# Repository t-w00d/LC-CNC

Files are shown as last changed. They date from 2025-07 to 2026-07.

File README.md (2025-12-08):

# Low-Cost CNC Desktop Milling Machine
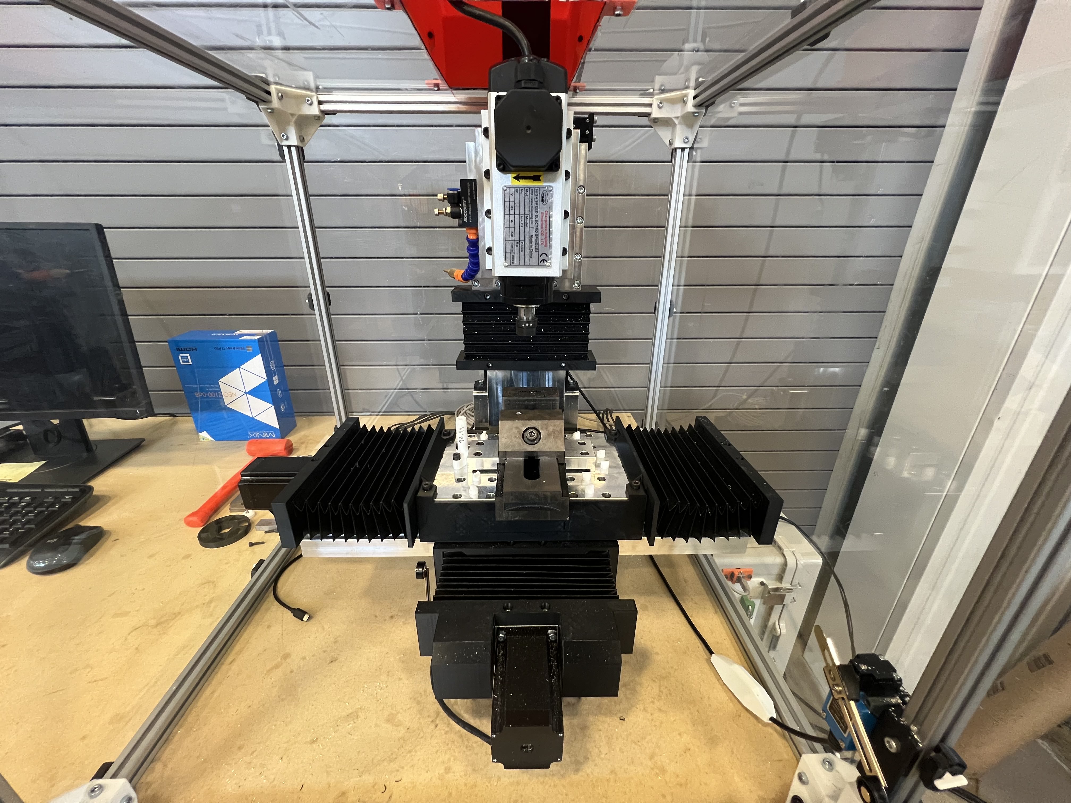
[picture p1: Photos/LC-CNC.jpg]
LC CNC Photo

# 

# |LC-CNC|

# This repository contains all necessary design files, instruction documents, and software binaries to build and run a low-cost desktop CNC machine. It includes: 

# \- Mechanical/Electrical design (SolidWorks files)
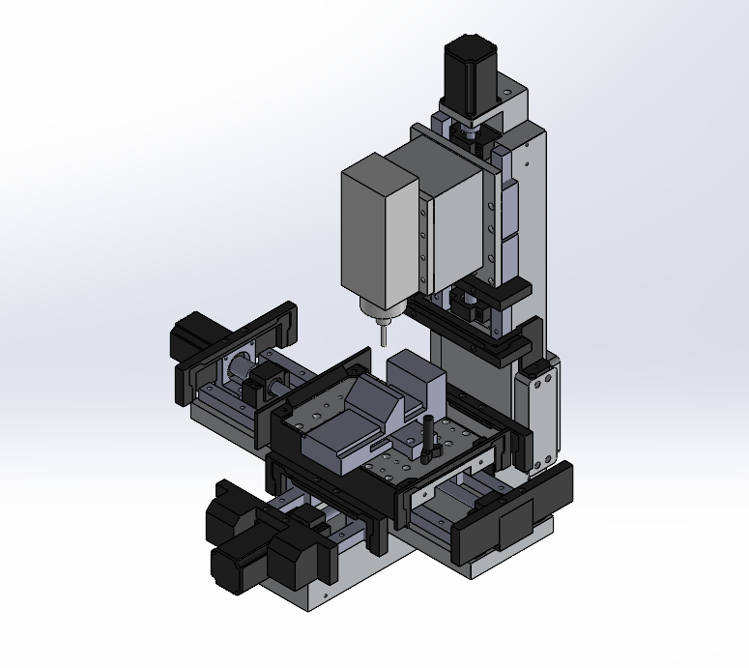
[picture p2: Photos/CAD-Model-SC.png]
CAD Model

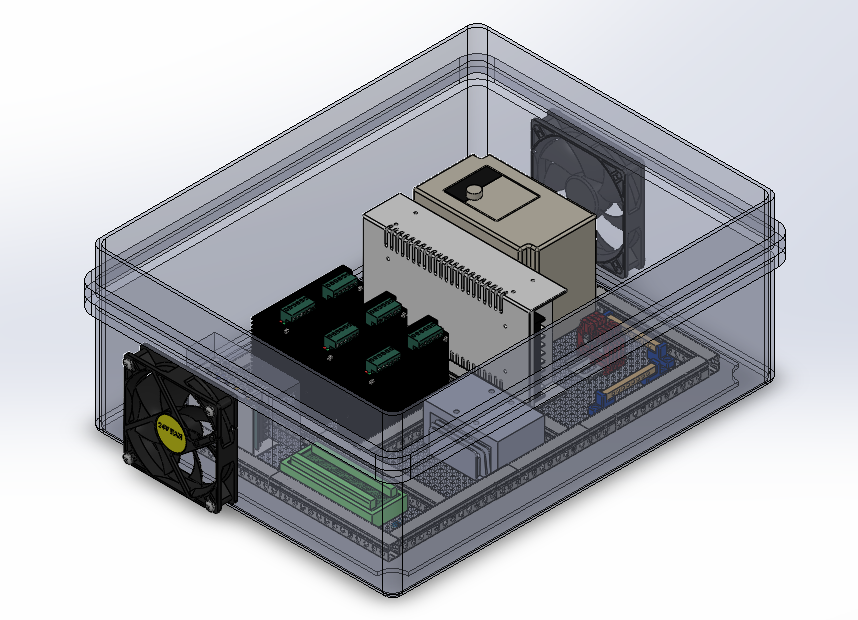
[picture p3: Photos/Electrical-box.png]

# \- Assembly + wiring instructions
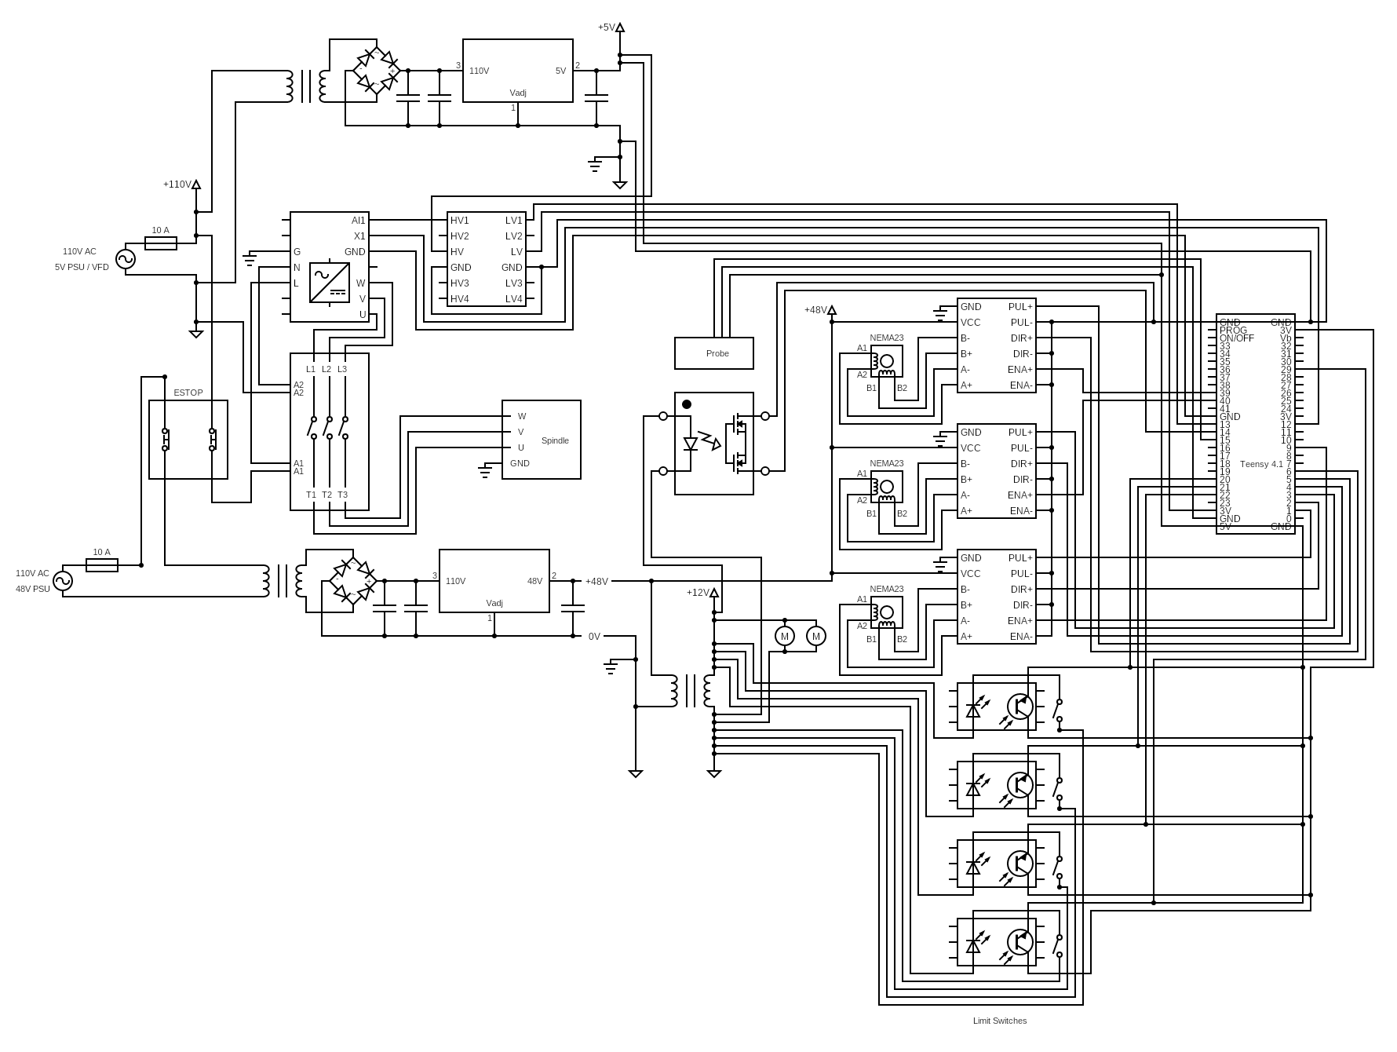
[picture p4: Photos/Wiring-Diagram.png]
Wiring Diagram

# \- Open-source firmware and control software for ease of use
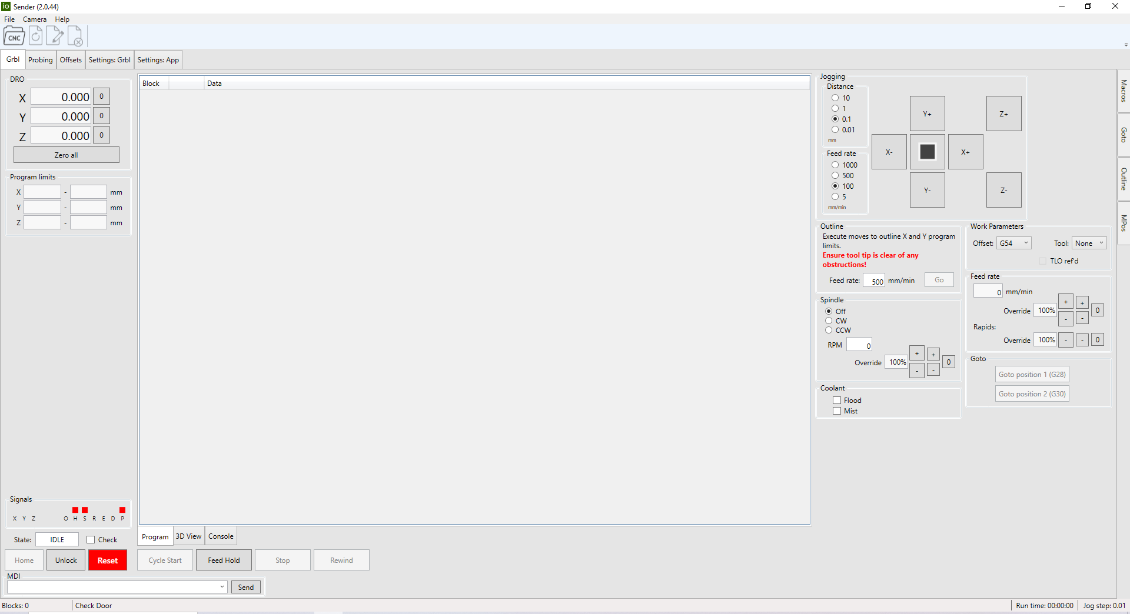
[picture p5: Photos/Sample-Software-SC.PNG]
Sender Software

# \- Educational curriculum tailored for the machine
# \- Bill of Materials
# \- Performance evaluations (error motions and circle-diamond-square)
# \- User manuals and datasheets

# |Specs|
# Current version uses machined 6061-T6 aluminum for the base, saddle, and column
# Driven by NEMA 23 motors with 2.45 N-m holding torque and DM556/DM566 drivers
# Motion system includes 16 mm ball screws and HGR20 linear rails for all axes
# 2.2 kW air-cooled spindle requires a VFD but runs on standard 110 V supply
# Controller is a Teensy 4.1 running GRBLHAL for machine control and compensation
# Machine footprint is roughly 660 mm x 660 mm
# Work volume: 152 mm x 254 mm x 152 mm 

# |Purchasing| (CNC-BoM.xlsx.)

# - All Machine/Electrical Components are required for the assembly of the LC-CNC

#	NOTE: The link to the carts are provided for ease of purchase when possible

# - All tools are required for successful assembly of the LC-CNC 

#	NOTE: Most tools are standard so only buy the specific tools you do not own

# - Recommendations are optional and only slightly improve user experience

#	NOTE: The table for the machine must be able to support 150lbs.

#	NOTE: Computer requirements: OS-Windows 10/11; Must have an ethernet port

#

# |Downloads|

# To avoid the need to navigate external GitHub repositories, the following software is bundled in the `binaries/` folder:

# -teensy.exe
# -ioSender.XL.2.0.46.zip
# -firmware.hex

# Download these versions that are known to work with the mechanical and electrical configuration provided in this repository. No modifications were made to the source code.

#

# |Getting Started|

# 1\. Purchase necessary items from CNC-BoM.xlsx.

# 2\. Assemble your machine using the instructions

# 3\. Flash `.hex` to your Teensy 4.1 using any Teensy-compatible flashing tool (teensy.exe)

# 4\. Download and extract `ioSender` from the provided ZIP

# 5\. Connect to your machine, configure settings, and start cutting! 

#

# |Educational Use|

# This project is tailored for use in schools, makerspaces, and research labs. The provided curriculum aligns with design and performance of this specific machine.

# We welcome improvements to documentation or curriculum under the same license terms.

#

# |License|

# All original work in this repository (CAD files, documentation, and curriculum) is licensed under the \*\*Creative Commons Attribution-NonCommercial-ShareAlike 4.0 International License (CC BY-NC-SA 4.0)\*\*.

# Read the full license terms here: https://creativecommons.org/licenses/by-nc-sa/4.0/ 

#

# |Third-Party Software|

# See `THIRD\_PARTY\_LICENSES.txt` for licensing details of the included firmware and sender application.

# \- grblHAL (GPL-3.0+)

# https://github.com/grblHAL

# \- ioSender (BSD-3-Clause)

# https://github.com/terjeio/ioSender

#

# |Credits|

# \- Original mechanical design and curriculum by Tyler Woodard, John Greene, and Colby Hale

# \- Firmware and sender software by Terje Io

# 

# Please respect original licenses when redistributing.

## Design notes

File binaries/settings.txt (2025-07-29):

%
;
; 2025-07-28T14:59
;
; grblHAL
; 1.1f.20250611
; [OPT:VNMSL+,100,1024,3,0]
; [NEWOPT:ENUMS,RT+,HOME,PROBES=1,ES,REBOOT,SED,ETH]
; [FIRMWARE:grblHAL]
; [NVS STORAGE:*FLASH]
; [FREE MEMORY:480K]
; [DRIVER:iMXRT1062]
; [DRIVER VERSION:250528]
; [DRIVER OPTIONS:USB.1]
; [BOARD:T41U5XBB]
; [AUX IO:6,3,0,0]
; [IP:169.254.28.238]
; [NETCON:Telnet]
;
$N0=
$N1=
; 0 - Step pulse time
$0=10.0
; 1 - Step idle delay
$1=25
; 2 - Step pulse invert
$2=0
; 3 - Step direction invert
$3=0
; 4 - Invert stepper enable output(s)
$4=7
; 5 - Invert limit inputs
$5=7
; 6 - Invert probe inputs
$6=1
; 9 - PWM spindle options
$9=1
; 10 - Status report options
$10=511
; 11 - Junction deviation
$11=0.010
; 12 - Arc tolerance
$12=0.002
; 13 - Report in inches
$13=0
; 14 - Invert control inputs
$14=8
; 15 - Invert coolant outputs
$15=0
; 16 - Invert spindle signals
$16=0
; 17 - Pullup disable control inputs
$17=0
; 18 - Pullup disable limit inputs
$18=0
; 19 - Pullup disable probe inputs
$19=0
; 20 - Soft limits enable
$20=0
; 21 - Hard limits enable
$21=0
; 22 - Homing cycle
$22=1
; 23 - Homing direction invert
$23=0
; 24 - Homing locate feed rate
$24=100.0
; 25 - Homing search seek rate
$25=500.0
; 26 - Homing switch debounce delay
$26=250
; 27 - Homing switch pull-off distance
$27=12.700
; 28 - G73 Retract distance
$28=0.100
; 29 - Pulse delay
$29=0.0
; 30 - Maximum spindle speed
$30=24000.000
; 31 - Minimum spindle speed
$31=0.000
; 32 - Mode of operation
$32=0
; 33 - Spindle PWM frequency
$33=5000
; 34 - Spindle PWM off value
$34=0.0
; 35 - Spindle PWM min value
$35=0.0
; 36 - Spindle PWM max value
$36=100.0
; 37 - Steppers to keep enabled
$37=0
; 39 - Enable legacy RT commands
$39=1
; 40 - Limit jog commands
$40=0
; 41 - Parking cycle
$41=0
; 42 - Parking axis
$42=2
; 43 - Homing passes
$43=1
; 44 - Axes homing, first pass
$44=4
; 45 - Axes homing, second pass
$45=3
; 46 - Axes homing, third pass
$46=0
; 56 - Parking pull-out distance
$56=5.0
; 57 - Parking pull-out rate
$57=100.0
; 58 - Parking target
$58=-5.0
; 59 - Parking fast rate
$59=500.0
; 60 - Restore overrides
$60=0
; 61 - Safety door options
$61=0
; 62 - Sleep enable
$62=0
; 63 - Feed hold actions
$63=3
; 64 - Force init alarm
$64=0
; 65 - Probing options
$65=0
; 70 - Network Services
$70=1
; 100 - X-axis travel resolution
$100=640.000
; 101 - Y-axis travel resolution
$101=640.000
; 102 - Z-axis travel resolution
$102=640.000
; 110 - X-axis maximum rate
$110=7500.000
; 111 - Y-axis maximum rate
$111=7500.000
; 112 - Z-axis maximum rate
$112=7500.000
; 120 - X-axis acceleration
$120=250.000
; 121 - Y-axis acceleration
$121=250.000
; 122 - Z-axis acceleration
$122=250.000
; 130 - X-axis maximum travel
$130=200.000
; 131 - Y-axis maximum travel
$131=200.000
; 132 - Z-axis maximum travel
$132=200.000
; 160 - X-axis backlash compensation
$160=0.013
; 161 - Y-axis backlash compensation
$161=0.013
; 162 - Z-axis backlash compensation
$162=0.000
; 300 - Hostname
$300=grblHAL
; 301 - IP Mode
$301=0
; 302 - IP Address
$302=169.254.28.238
; 303 - Gateway
$303=169.254.28.1
; 304 - Netmask
$304=255.255.0.0
; 305 - Telnet port
$305=23
; 307 - Websocket port
$307=80
; 341 - Tool change mode
$341=0
; 342 - Tool change probing distance
$342=30.0
; 343 - Tool change locate feed rate
$343=25.0
; 344 - Tool change search seek rate
$344=200.0
; 345 - Tool change probe pull-off rate
$345=200.0
; 346 - Tool change options
$346=1
; 370 - Invert I/O Port inputs
$370=0
; 372 - Invert I/O Port outputs
$372=0
; 384 - Disable G92 persistence
$384=0
; 392 - Spindle on delay
$392=4.0
; 393 - Coolant on delay
$393=1.0
; 394 - Spindle on delay
$394=0.0
; 398 - Planner buffer blocks
$398=100
; 481 - Autoreport interval
$481=0
; 484 - Unlock required after E-Stop
$484=0
; 486 - Lock coordinate systems
$486=0
; 539 - Spindle off delay
$539=0.0
; 673 - Coolant on delay
$673=0.0
; 676 - Reset actions
$676=3
; 680 - Stepper enable delay
$680=0
%

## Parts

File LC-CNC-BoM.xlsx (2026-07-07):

Machine/Electrical Components: |  | Number of Machines: |  |  | 1 | Tools | NOTE: Only one set of tools needed
Item | Link | Status | Quantity | Price/Item | Total Price | Item | Link | Status | Quantity | Price/Item | Total Price
Makerstore |  |  |  |  |  | Amazon
Shielded 4 Core Cable – 22AWG | https://makerstore.cc/product/elec-cable-4s-xtension/ | In Stock | 15 | $3.33 | $49.95 | Ferrule crimping tool | https://www.amazon.com/Klein-Tools-34056-Adjustable-Electrical/dp/B0D98N52HS | In Stock | 1 | $20.99 | $20.99
Shielded 2 Core Cable – 22AWG | https://makerstore.cc/product/elec-cable-2s-xtension/ | In Stock | 15 | $1.73 | $25.95 | Ferrule connectors | https://www.amazon.com/Fidioto-Terminals-Connector-Insulated-Industrial/dp/B09XQN3J6N?s=industrial | In Stock | 1 | $14.99 | $14.99
Amazon |  |  |  |  |  | Soldering iron | https://www.amazon.com/gp/product/B0CJR4Y192/ref=ox_sc_act_title_2?smid=A1NCCSMTWFDZ34&psc=1 | In Stock | 1 | $19.99 | $19.99
110v Spindle Motor Kit，2.2Kw Square Air Cooled Spindle Motor 24000Rpm 400Hz ，VFD Variable Frequency Drive ，7 pcs ER11 Collets | https://a.co/d/04KkNO5x | In Stock | 1 | $359.99 | $359.99 | Solder | https://www.amazon.com/MAIYUM-63-37-Solder-Electrical-Soldering/dp/B075WB98FJ?s=hi | In Stock | 1 | $8.99 | $8.99
16awg 4 core wire 12ft | https://www.amazon.com/Shielded-Extreme-Flexible-Electrical-Machine/dp/B0C1YH4J1T | In Stock | 1 | $30.99 | $30.99 | Heat shrink | https://www.amazon.com/Ginsco-580-pcs-Assorted-Sleeving/dp/B01MFA3OFA?s=industrial | In Stock | 1 | $6.99 | $6.99
 |  |  |  |  |  | Heat gun | https://www.amazon.com/Wagner-Spraytech-2417344-Included-Settings/dp/B08RHDWTW1?s=industrial | In Stock | 1 | $27.99 | $27.99
Way Covers | https://www.amazon.com/dp/B07BXK6BYS?s=hi&sp_csd=d2lkZ2V0TmFtZT1zcF9kZXRhaWw | In Stock | 4 | $20.18 | $80.72 | Manual Wire stripper | https://www.amazon.com/VISE-GRIP-Stripping-Cutter-8-Inch-2078309/dp/B000JNNWQ2?s=industrial | In Stock | 1 | $13.33 | $13.33
Air blast | https://www.amazon.com/Upgrade-Version-Coolant-Lubrication-Engraving/dp/B07X89Z1W9?hvadid=616989210950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 | In Stock | 1 | $18.88 | $18.88 | Crimp tool | https://www.amazon.com/Haisstronica-Electrical-Connectors-AWG-Tools-Racheting-Tools-Available/dp/B08F3JKDD3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 | In Stock | 1 | $18.69 | $18.69
5 Pin connector | https://www.amazon.com/DaFurui-5-08mm-Screw%EF%BC%8C10Pcs-Terminal-Connector/dp/B0C2XZFR1J?s=industrial | In Stock | 1 | $16.99 | $16.99 | Stub Allen Key set | https://www.amazon.com/Powerbuilt-Piece-Stubby-Long-Wrench/dp/B07N8F7W7K | In Stock | 1 | $24.99 | $24.99
3 Pin connector | https://www.amazon.com/DaFurui-5-08mm-Screw%EF%BC%8C10Pcs-Terminal-Connector/dp/B0C2Y2V78Y?s=industrial | In Stock | 1 | $16.99 | $16.99 | Screw driver set | https://www.amazon.com/Amazon-Basics-Ratcheting-Electronics-Screwdriver/dp/B07V4TFWFZ?s=industrial | In Stock | 1 | $15.09 | $15.09
Loctite-Blue | https://www.amazon.com/Loctite-Heavy-Duty-Threadlocker-Single/dp/B000I1RSNS | In stock | 1 | $7.24 | $7.24 | Automatic Wire stripper | https://www.amazon.com/WEICON-Stripper-Adjustable-0-2-6-0-Stripping/dp/B001NUMVHQ | In Stock | 1 | $25.50 | $25.50
Touch Probe | https://www.amazon.com/V5-Waterproof-Anti-roll-Compatible-Finder-NO/dp/B0BDSDSJF6 | In stock | 1 | $67.99 | $67.99 | Compressor | https://www.amazon.com/Milwaukee-M12-Lithium-Ion-Cordless-Kit/dp/B07J1DCM59?s=hi | In Stock | 1 | $162.00 | $162.00
Ethernet cable | https://www.amazon.com/Amazon-Basics-Ethernet-High-Speed-Snagless/dp/B089MGH8W3?s=electronics | In Stock | 1 | $6.39 | $6.39 | Magnets | https://www.amazon.com/AplysiaTech-N52-3-Powerful-Neodymium-Scientific/dp/B0DC65Z3SF?ref_=ast_sto_dp | In Stock | 1 | $23.99 | $23.99
Fans | https://www.amazon.com/Strong-120x120x25mm-Computer-Cooling-1600RPM/dp/B07D493BDX | In Stock | 1 | $12.99 | $12.99 | Ferrite beads | https://www.amazon.com/HUAREW-Values-Ferrite-Suppressor-Diameter/dp/B09SWNPY2Y | In Stock | 1 | $13.99 | $13.99
Limit Switches | https://www.amazon.com/dp/B07PZ1WB8S?psc=1&smid=A26VZBPE6PT1GF&ref_=chk_typ_imgToDp | In Stock | 1 | $9.99 | $9.99 | Hammer | https://www.amazon.com/Neiko-02846A-Hammer-Orange-Handle/dp/B002GQ967Y?ref_=ast_sto_dp&th=1 | In Stock | 1 | $12.81 | $12.81
PSU 0-48v 0-10A | https://www.amazon.com/DROK-110V-220V-Converter-Adjustable-Transformer/dp/B08GFQZFC1?s=electronics | In Stock | 1 | $39.99 | $39.99 | Multimeter | https://www.amazon.com/Klein-Tools-MM325-Multimeter-Manual-Ranging/dp/B0B57L9FNL | In Stock | 1 | $34.97 | $34.97
300mm Ball screw | https://www.amazon.com/CHUANGNENG-Deflector-Supports-HOUSINGS-Machining/dp/B089DF7P6R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 | 4 In Stock (4-13-25) | 2 | $34.69 | $69.38 | McMaster Carr
450mm Ball screw | https://www.amazon.com/CHUANGNENG-Deflector-Supports-HOUSINGS-Machining/dp/B089DGRFY9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 | 8 In Stock (4-13-25) | 1 | $40.39 | $40.39 | T handle | https://www.mcmaster.com/5374A56/ | In Stock | 1 | $9.54 | $9.54
48v to 12v step down | https://www.amazon.com/KInuoxj-Converter-Regulator-Waterproof-Transformer/dp/B0CS2KJSKS | In Stock | 1 | $16.99 | $16.99 | Grease gun | https://www.mcmaster.com/1190K37/ | In Stock | 1 | $41.86 | $41.86
4pcs 8 position grounding bar | https://www.amazon.com/gp/product/B0CYHH6ZPM/ref=ewc_pr_img_8?smid=A2UXHIGK0EM1ZO&psc=1 | In Stock | 1 | $8.99 | $8.99 | Wire Stripper | https://www.mcmaster.com/7312K11/ | In Stock | 1 | $36.15 | $36.15
4 pack DM566 drivers | https://www.amazon.com/Digital-Stepper-Controller-2-Phase-Subdivision/dp/B0CN41Y4DJ | 11 In Stock (4-13-25) | 1 | $48.99 | $48.99 | Allen key set | https://www.mcmaster.com/5709A44/ | In Stock | 1 | $7.55 | $7.55
300PCS Electrical Connectors Kit, | https://www.amazon.com/gp/product/B086ZP4N7K/ref=ox_sc_act_title_7?smid=AON9H44N0KDA1&th=1 | In Stock | 1 | $8.99 | $8.99 | MSC
3'' Precision Screwless Vise | https://www.amazon.com/AccusizeTools-Precision-Screwless-Hardened-0235-0303/dp/B00UCHGLUO | 16 In Stock (4-13-25) | 1 | $124.00 | $124.00 | 1-2-3 setup block | https://www.mscdirect.com/product/details/03433620 | In Stock | 1 | $55.35 | $55.35
Roller arm Limit Switches | https://a.co/d/0cbCCCRe | In Stock | 2 | $8.99 | $17.98 | Square Steel Gage: .35 in | https://www.mscdirect.com/product/details/86274404 | In Stock | 1 | $35.76 | $35.76
 |  |  |  |  |  | Square Steel Gage: .13 in | https://www.mscdirect.com/product/details/86272507 | In Stock | 1 | $30.07 | $30.07
 |  |  |  |  |  | Gage pin | https://www.mscdirect.com/product/details/89024806 | In Stock | 1 | $3.80 | $3.80
22awg wire | https://www.amazon.com/TYUMEN-Hookup-Electrical-Strips-Extension/dp/B07SLBD1FY?s=industrial | In Stock | 1 | $15.99 | $15.99 | Indicator positioner | https://www.mscdirect.com/product/details/94110061 | In Stock | 1 | $87.75 | $87.75
Logic level shifter | https://www.amazon.com/HiLetgo-Channels-Converter-Bi-Directional-3-3V-5V/dp/B07F7W91LC?s=industrial | In Stock | 1 | $7.69 | $7.69 | Calipers | https://www.mscdirect.com/product/details/62529482 | In Stock | 1 | $148.53 | $148.53
Heat set assortment | https://www.amazon.com/dp/B08ZJ6HNGK?ref_=ppx_hzsearch_conn_dt_b_fed_asin_title_1&th=1 | In Stock | 1 | $11.47 | $11.47 | Indicator | https://www.mscdirect.com/product/details/38353306 | In Stock | 1 | $171.00 | $171.00
10A 16awg fuse | https://www.amazon.com/16-AWG-Inline-Fuse-Holder/dp/B08K3NFZCP?ref_=ast_sto_dp&th=1 | In Stock | 1 | $12.99 | $12.99 | Shop vac | https://www.mscdirect.com/product/details/16520850 | In Stock | 1 | $84.66 | $84.66
Optocoupler Isolation Board | https://www.amazon.com/dp/B07TCVTD2K?ref=ppx_yo2ov_dt_b_fed_asin_title&th=1 | In Stock | 1 | $7.99 | $7.99 | Parallel set | https://www.mscdirect.com/product/details/06820898 | In Stock | 1 | $102.36 | $102.36
1CH Optocoupler isolation board | https://www.amazon.com/dp/B01L1OI1HC?ref_=ppx_hzsearch_conn_dt_b_fed_asin_title_4&th=1 | In Stock | 1 | $13.99 | $13.99 | Total |  |  |  |  | $1259.68
L Connector brackets | https://www.amazon.com/gp/product/B0BY51FJGY/ref=ewc_pr_img_1?smid=AO6JMNGOG26ZH&th=1 | In Stock | 2 | $19.99 | $39.98
5V Power Supply | https://www.amazon.com/Universal-Regulated-Switching-Converter-Transformer/dp/B07PPPF1R5 | In Stock | 1 | $10.07 | $10.07 | Crank Slider Stock | NOTE: This qty will make 16 assemblies
4 Pin Terminal Block | https://a.co/d/07VW1Jxs | In Stock | 1 | $9.99 | $9.99 | Item | Link | Status | Quantity | Price/Item | Total Price
NEMA 23 Stepper motor 3N-m | https://www.amazon.com/gp/product/B00PNEPW4C/ref=ox_sc_act_title_22?smid=AWQBCGWISS7BL&psc=1 | In Stock | 1 | $39.99 | $39.99 | McMaster
NEMA 23 Stepper motor 2.4N-m | https://a.co/d/0cYAOFF7 | In Stock | 2 | $25.99 | $51.98 | Base Stock 4ft | https://www.mcmaster.com/8662K88/ | In Stock | 1 | $77.32 | $77.32
8mm to 10mm Shaft Coupling | https://a.co/d/0c78GAUY | In Stock | 1 | $12.99 | $12.99 | Crank Stock 3ft | https://www.mcmaster.com/8975K12-8975K123/ | In Stock | 1 | $22.81 | $22.81
Teensy 4.1 Ethernet Kit | https://a.co/d/04Kofe6e | In Stock | 1 | $13.95 | $13.95 | Slider Stock 3ft | https://www.mcmaster.com/9008K11-9008K113/ | In Stock | 1 | $16.12 | $16.12
Teensy 4.1 Conrtoller | https://www.amazon.com/gp/product/B08CTM3279/ref=ox_sc_act_title_5?smid=A2GTSJRNFEVVSP&psc=1 | In Stock | 1 | $44.15 | $44.15 | ER20 Collet - 1/4 in | https://www.mcmaster.com/1724N17/ | In Stock | 1 | $53.00 | $53.00
10mm to 10mm Shaft Coupling | https://a.co/d/0aCp7x5M | In Stock | 1 | $12.99 | $12.99 | ER20 Collet - 1/8 in | https://www.mcmaster.com/1724N13/ | In Stock | 1 | $53.00 | $53.00
Digikey |  |  |  |  |  | MSC
2 Pin PCB terminal block | https://www.digikey.com/en/products/detail/w-rth-elektronik/691210910002/10668428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 | In Stock | 10 | $0.89 | $8.86 | 1/8th inch square endmill | https://www.mscdirect.com/product/details/65249682 | In Stock | 2 | $19.63 | $39.26
McMaster Carr |  |  |  |  |  | 1/4th inch square endmill | https://www.mscdirect.com/product/details/82976580 | In Stock | 2 | $28.81 | $57.62
IEC Receptical | https://www.mcmaster.com/5428N111/ | In Stock | 2 | $14.77 | $29.54 | Total: |  |  |  |  | $319.13
IEC Cable | https://www.mcmaster.com/71535K51/ | In Stock | 2 | $7.80 | $15.60
Hinges | https://www.mcmaster.com/6812N511/ | In Stock | 2 | $13.05 | $26.10 | Recommendedations | NOTE: Computer must have ethernet
EP1 Grease | https://www.mcmaster.com/1416K41/ | In Stock | 1 | $9.01 | $9.01 | Item | Link | Status | Quantity | Price/Item | Total Price
Vibration-Damping Sandwich Mount with Stud&Insert | https://www.mcmaster.com/93945K155/ | In Stock | 4 | $3.81 | $15.24 | McMaster
Touch plate screw | https://www.mcmaster.com/99607A263/ | In Stock | 1 | $5.29 | $5.29 | Table option 1 | https://www.mcmaster.com/6682T93/ | In Stock | 1 | $721.96 | $721.96
T-Nuts | https://www.mcmaster.com/5537T651/ | In Stock | 10 | $4.18 | $41.80 | MSC
Polycarbonate sheet | https://www.mcmaster.com/8574K53/ | In Stock | 2 | $30.67 | $61.34 | Table option 2 | https://www.mscdirect.com/product/details/51724680 | In Stock | 1 | $367.84 | $367.84
M5x12 mm bolts | https://www.mcmaster.com/90128A236/ | In Stock | 2 | $9.55 | $19.10 | Best Buy
M5x16 mm bolts | https://www.mcmaster.com/91290A232/ | In Stock | 1 | $16.87 | $16.87 | Computer | https://www.bestbuy.com/site/minix-z100-0db-fanless-mini-pc-intel-12th-gen-n100-16gb-ddr4-512gb-pcie-gen3-x-4-nvme-ssd-windows-11-pro-desktop-computer-black/6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 | In Stock | 1 | $239.99 | $239.99
1/4-20 bolts -1.25in | https://www.mcmaster.com/90128A250/ | In Stock | 1 | $8.33 | $8.33 | Total: |  |  |  |  | $961.95
1/4-20 bolts -1-5/8in | https://www.mcmaster.com/91251A527/ | In Stock | 1 | $20.87 | $20.87
1/4-20 bolts -.75in | https://www.mcmaster.com/91251A540/ | In Stock | 2 | $11.38 | $22.76 | Stock material | NOTE: Local metal supplier to UTK; Price per 1 machine
M5x25 mm bolts | https://www.mcmaster.com/91290A252/ | In Stock | 1 | $10.71 | $10.71 | Item | Link | Status | Quantity | Price/Item | Total Price
1/4-20 bolts -1in | https://www.mcmaster.com/91251A542/ | In Stock | 1 | $12.36 | $12.36 | Specialty Metals
M5x40 mm bolts | https://www.mcmaster.com/91290A196/ | In Stock | 1 | $7.78 | $7.78 | 6061 1" x 6" | N/a | In Stock | 1 | $135.00 | $135.00
M3x10mm | https://www.mcmaster.com/91290A115/ | In Stock | 1 | $12.92 | $12.92 | 6061 2.5" x 5" | N/a | In Stock | 1 | $280.00 | $280.00
M3x10mm self tap | https://www.mcmaster.com/99461A942/ | In Stock | 1 | $8.00 | $8.00 | 6061 3.5" x 6" | N/a | In Stock | 1 | $102.00 | $102.00
M4x16 mm | https://www.mcmaster.com/91290A154/ | In Stock | 1 | $13.40 | $13.40 | Total: |  |  |  |  | $517.00
M4 hex nut | https://www.mcmaster.com/90591A255/ | In Stock | 1 | $3.11 | $3.11
M5 hex nut | https://www.mcmaster.com/90591A260/ | In Stock | 1 | $3.56 | $3.56 | Safety Stickers/PPE | NOTE: This qty is for 15 machines
#6 screws | https://www.mcmaster.com/90031A151/ | In Stock | 1 | $6.69 | $6.69 | Item | Link | Status | Quantity | Price/Item | Total Price
Twin ferrule assortment | https://www.mcmaster.com/9689K13/ | In Stock | 1 | $27.76 | $27.76 | MySafetyLabels
Shim stock | https://www.mcmaster.com/9504K321/ | In Stock | 1 | $15.31 | $15.31 | 1.5" x 3" ANSI Caution Safety Label: Eye protection required. (LB-0321) | https://www.mysafetylabels.com/msl/caution-eye-protection-required-safety-label/sku-lb-0321 | In Stock | 15 | $2.32 | $34.80
Washer assortment | https://www.mcmaster.com/91535A200/ | In Stock | 1 | $20.00 | $20.00 | 1.5" x 3" Hand Cut Warning Label: Moving Parts Can Crush And Cut, Do Not Operate With Guard Removed, Lockout/Tagout Before Servicing (LB-0231) | https://www.mysafetylabels.com/warning-labels/rotating-cutter-safety-label/sku-lb-0199 | In Stock | 15 | $2.32 | $34.80
Steel DIN 3 Rail, 2" Length | https://www.mcmaster.com/8961K84/ | In Stock | 1 | $3.90 | $3.90 | .75" x .84" ANSI Z535.4 and ISO 3864-2 Warning (Triangle) Safety Label: ISO W017 - Burn Hazard / Hot Surface (LB-0290) | https://www.mysafetylabels.com/warning-labels/burn-hazard-hot-surface-safety-label/sku-lb-0290 | In Stock | 24 | $1.79 | $42.96
Black DIN-Rail Terminal Block | https://www.mcmaster.com/7641K921-7641K929/ | In Stock | 2 | $2.34 | $4.68 | 1.5" x 3" ANSI Warning Label: Do Not Open | https://www.mysafetylabels.com/do-not-open-while-machine-is-in-operation-warning-label/sku-lb-2432 | In Stock | 15 | $2.32 | $34.80
Orange DIN-Rail Terminal Block | https://www.mcmaster.com/7641K921-7641K928/ | In Stock | 3 | $2.34 | $7.02 | 2"x 3" ANSI Z535.4 and ISO 3864-2 Warning (Triangle) Safety Label: ISO W012 - Electrical Shock / Electrocution (LB-0012) | https://www.mysafetylabels.com/115-volts-ansi-danger-label/sku-lb-2396-115 | In Stock | 24 | $1.11 | $26.64
Yellow DIN-Rail Terminal Block | https://www.mcmaster.com/7641K921-7641K927/ | In Stock | 3 | $2.34 | $7.02 | ULINE
White DIN-Rail Terminal Block | https://www.mcmaster.com/7641K921-7641K926/ | In Stock | 2 | $2.34 | $4.68 | Safety glasses | https://www.uline.com/Product/Detail/S-13390C/Safety-Glasses/Ice-Wraparounds-Clear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 | In Stock | 15 | $2.50 | $37.50
Wire ducts | https://www.mcmaster.com/7578K112-7578K725/ | In Stock | 1 | $23.68 | $23.68 | Lockout Tagout | https://www.uline.com/Product/Detail/H-3437/Lockout-Tagout/Electrical-Plug-Prong-Lockout | In Stock | 8 | $14.00 | $112.00
Zip tie anchor | https://www.mcmaster.com/7566K205/ | In Stock | 1 | $15.54 | $15.54 | Padlock | https://www.uline.com/Product/Detail/H-8621R/Lockout-Tagout/Uline-Lockout-Padlock-Keyed-Different-1-1-2-Shackle-Red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 | In Stock | 8 | $11.00 | $88.00
Cord grip | https://www.mcmaster.com/69915K53/ | In Stock | 2 | $4.79 | $9.58 | Total: |  |  |  |  | $411.50
Green 22 AWG Wire: Solid Core | https://www.mcmaster.com/8251T2-8251T351/ | In Stock | 1 | $3.64 | $3.64
Red 22 AWG Wire: Solid Core | https://www.mcmaster.com/8251T2-8251T391/ | In Stock | 1 | $3.64 | $3.64
Blue 22 AWG Wire: Solid Core | https://www.mcmaster.com/8251T2-8251T321/ | In Stock | 1 | $3.64 | $3.64
Orange 22 AWG Wire: Solid Core | https://www.mcmaster.com/8251T2-8251T371/ | In Stock | 1 | $3.64 | $3.64
Black 16 AWG Wire: Stranded | https://www.mcmaster.com/8054T16-8054T317/ | In Stock | 1 | $15.26 | $15.26
Red 16 AWG Wire: Stranded | https://www.mcmaster.com/8054T16-8054T361/ | In Stock | 1 | $8.16 | $8.16
White 16 AWG Wire: Stranded | https://www.mcmaster.com/8054T16-8054T366/ | In Stock | 1 | $8.16 | $8.16
Green 16 AWG Wire: Stranded | https://www.mcmaster.com/8054T16-8054T338/ | In Stock | 1 | $8.16 | $8.16
Emergency Stop | https://www.mcmaster.com/6785K22/ | In Stock | 1 | $85.17 | $85.17
80/20
20-2020 LENGTH: 596.6 millimeters | https://8020.net/20-2020.html | In Stock | 8 | $9.07 | $72.56
20-2020 LENGTH: 636.6 millimeters | https://8020.net/20-2020.html | In Stock | 4 | $9.49 | $37.96
20-2020 LENGTH: 593.6 millimeters | https://8020.net/20-2020.html | In Stock | 2 | $9.04 | $18.08
20-2020 LENGTH: 553.6 millimeters | https://8020.net/20-2020.html | In Stock | 2 | $8.63 | $17.26
14157 LENGTH: 8 meters | https://8020.net/14157.html | In Stock | 1 | $28.24 | $28.24
CZH-LABS
Breakout board | https://czh-labs.com/products/terminal-block-breakout-board-module-for-teensy-41-screw-mount-version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 | In Stock | 1 | $20.90 | $20.90
Grainger
DAYTON Definite Purpose Magnetic Contactor | https://www.grainger.com/product/DAYTON-Definite-Purpose-Magnetic-783Y04 | In stock | 1 | $30.21 | $30.21
Component Total: |  |  |  |  | $2270.06
Component Total per machine: |  |  |  |  | $2270.06
Total per machine: |  |  |  |  | $2787.06

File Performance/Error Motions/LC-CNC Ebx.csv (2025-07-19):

Title | MiniMill Exy
Operator | 88h
Date | 9/23/2024 10:00
Machine information
Name | OpenSource MiniMill
Serial number | 1
Axis under test | X
Test method
Target sequence | Linear
Run sequence | Alternate
Run type | Bidirectional
Targets/Run | 12
Number of runs | 3
Number of channels | 1
XRY | microradians
Index | Targets (mm) | Run 1 (+) Error | Run 1 (+) Time stamp | Run 1 (-) Error | Run 1 (-) Time stamp | Run 2 (+) Error | Run 2 (+) Time stamp | Run 2 (-) Error | Run 2 (-) Time stamp | Run 3 (+) Error | Run 3 (+) Time stamp | Run 3 (-) Error | Run 3 (-) Time stamp
1 | -220 | 5.1 | 10:00:06 AM | -0.7 | 10:02:53 AM | -0.7 | 10:03:00 AM | -1.3 | 10:06:19 AM | -1.6 | 10:06:27 AM | -0.9 | 10:08:50 AM
2 | -200 | 10.3 | 10:00:19 AM | 11.3 | 10:02:45 AM | 12.4 | 10:03:06 AM | 9.9 | 10:06:12 AM | 10.9 | 10:06:34 AM | 10.9 | 10:08:44 AM
3 | -180 | 43.9 | 10:00:25 AM | 40.6 | 10:02:37 AM | 41.6 | 10:03:15 AM | 42 | 10:06:00 AM | 42.2 | 10:06:39 AM | 39.3 | 10:08:38 AM
4 | -160 | 98.3 | 10:00:32 AM | 96.3 | 10:02:30 AM | 96.1 | 10:03:21 AM | 92 | 10:05:53 AM | 91.8 | 10:06:47 AM | 93.1 | 10:08:33 AM
5 | -140 | 144.7 | 10:00:39 AM | 139 | 10:02:24 AM | 143.3 | 10:03:28 AM | 138.7 | 10:05:45 AM | 138.5 | 10:06:54 AM | 135.4 | 10:08:27 AM
6 | -120 | 168.1 | 10:00:46 AM | 168.6 | 10:02:17 AM | 166.5 | 10:03:34 AM | 166.2 | 10:05:37 AM | 165.1 | 10:07:03 AM | 164 | 10:08:22 AM
7 | -100 | 184.5 | 10:00:53 AM | 184.4 | 10:02:09 AM | 182.5 | 10:03:38 AM | 182.4 | 10:05:30 AM | 184.9 | 10:07:15 AM | 182.6 | 10:08:16 AM
8 | -80 | 178.9 | 10:01:01 AM | 176.5 | 10:02:01 AM | 175.6 | 10:03:44 AM | 176.3 | 10:05:16 AM | 175.2 | 10:07:23 AM | 177.5 | 10:08:11 AM
9 | -60 | 146.2 | 10:01:09 AM | 143.1 | 10:01:54 AM | 142.2 | 10:03:50 AM | 139.7 | 10:05:02 AM | 139.2 | 10:07:29 AM | 138.5 | 10:08:05 AM
10 | -40 | 120.4 | 10:01:15 AM | 121.3 | 10:01:46 AM | 122.6 | 10:04:11 AM | 119.8 | 10:04:54 AM | 119.7 | 10:07:35 AM | 116.1 | 10:08:00 AM
11 | -20 | 72.9 | 10:01:20 AM | 70.6 | 10:01:40 AM | 69.8 | 10:04:24 AM | 67.5 | 10:04:42 AM | 68.3 | 10:07:40 AM | 65.6 | 10:07:56 AM
12 | 0 | -4.6 | 10:01:27 AM | -1.7 | 10:01:35 AM | 1.8 | 10:04:30 AM | 0.7 | 10:04:37 AM | 1.8 | 10:07:45 AM | 2 | 10:07:51 AM
Test equipment
Renishaw XL-80
Manufacturer | Renishaw plc
Model | Renishaw XL-80
Serial number | 2NMA84
Calibration date | 1/25/2021 0:00
Certificate number | 2NMA84-210125-00
Calibration organization | Renishaw Inc
Renishaw XC-80
Manufacturer | Renishaw plc
Model | Renishaw XC-80
Serial number | 2YNH13
Calibration date | 1/25/2021 0:00
Certificate number | 2YNH13-210125-00
Calibration organization | Renishaw PLC
AirTemperature
Manufacturer | Renishaw plc
Model | AirTemperature
Serial number | 23J127
Calibration date | 1/25/2021 0:00
Certificate number | 20210125-23J127-00
Calibration organization | Renishaw plc
AirPressure
Manufacturer | Renishaw plc
Model | AirPressure
Serial number | 23J081
Calibration date | 1/25/2021 0:00
Certificate number | 20210125-23J081-00
Calibration organization | Renishaw plc
MaterialTemperature1
Manufacturer | Renishaw plc
Model | MaterialTemperature1
Serial number | 23H984
Calibration date | 1/25/2021 0:00
Certificate number | 20210125-23H984-00
Calibration organization | Renishaw plc
Sensor | Start reading | End reading | Min reading | Max reading
Air temp [°C] | 23.3 | 23.3 | 23.2 | 23.3
Air pressure [mbar] | 975 | 975 | 975 | 975
Air humidity [%RH] | 60 | 60 | 60 | 60
Material temp 1 [°C] | 23.5 | 23.4 | 23.4 | 23.5
Material temp 2 [°C] | Not recorded | Not recorded
Material temp 3 [°C] | Not recorded | Not recorded

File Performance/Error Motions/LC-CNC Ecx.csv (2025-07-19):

Title | MiniMill Exz
Operator | 88h
Date | 9/23/2024 10:52
Machine information
Name | OpenSource MiniMill
Serial number | 1
Axis under test | X
Test method
Target sequence | Linear
Run sequence | Alternate
Run type | Bidirectional
Targets/Run | 12
Number of runs | 3
Number of channels | 1
XRZ | microradians
Index | Targets (mm) | Run 1 (+) Error | Run 1 (+) Time stamp | Run 1 (-) Error | Run 1 (-) Time stamp | Run 2 (+) Error | Run 2 (+) Time stamp | Run 2 (-) Error | Run 2 (-) Time stamp | Run 3 (+) Error | Run 3 (+) Time stamp | Run 3 (-) Error | Run 3 (-) Time stamp
1 | -220 | 2.9 | 10:52:54 AM | 2 | 10:56:11 AM | 0.7 | 10:56:29 AM | -2.5 | 10:58:42 AM | -2.8 | 10:58:49 AM | -0.3 | 11:00:54 AM
2 | -200 | 46.8 | 10:53:03 AM | 52.6 | 10:56:01 AM | 51.2 | 10:56:34 AM | 48.7 | 10:58:37 AM | 46.8 | 10:58:54 AM | 46.8 | 11:00:48 AM
3 | -180 | 78.8 | 10:53:09 AM | 78.6 | 10:55:53 AM | 76 | 10:56:40 AM | 77.2 | 10:58:32 AM | 74.7 | 10:58:59 AM | 73.3 | 11:00:43 AM
4 | -160 | 88.4 | 10:53:14 AM | 88.6 | 10:55:48 AM | 87.4 | 10:56:48 AM | 87.9 | 10:58:27 AM | 86.4 | 10:59:04 AM | 87.5 | 11:00:38 AM
5 | -140 | 96.6 | 10:53:20 AM | 97.4 | 10:55:23 AM | 93.7 | 10:56:54 AM | 89.2 | 10:58:22 AM | 87.6 | 10:59:09 AM | 90.5 | 11:00:33 AM
6 | -120 | 97 | 10:53:25 AM | 99.3 | 10:55:17 AM | 94.1 | 10:57:01 AM | 97.4 | 10:58:17 AM | 94.8 | 10:59:15 AM | 94.9 | 11:00:27 AM
7 | -100 | 99.3 | 10:53:29 AM | 95.7 | 10:54:56 AM | 92.4 | 10:57:07 AM | 97.3 | 10:58:11 AM | 90.5 | 10:59:20 AM | 93.9 | 11:00:21 AM
8 | -80 | 97.1 | 10:53:35 AM | 97.8 | 10:54:41 AM | 97.1 | 10:57:13 AM | 95.4 | 10:58:06 AM | 95.6 | 10:59:26 AM | 97.4 | 11:00:16 AM
9 | -60 | 88.8 | 10:53:40 AM | 91.2 | 10:54:21 AM | 83.4 | 10:57:18 AM | 86.5 | 10:58:00 AM | 84 | 10:59:31 AM | 86.7 | 11:00:10 AM
10 | -40 | 68.1 | 10:53:45 AM | 68.4 | 10:54:15 AM | 66.9 | 10:57:24 AM | 69.5 | 10:57:55 AM | 69.2 | 10:59:37 AM | 67.4 | 11:00:05 AM
11 | -20 | 38.8 | 10:53:51 AM | 40 | 10:54:11 AM | 37.7 | 10:57:31 AM | 38.1 | 10:57:49 AM | 33.5 | 10:59:42 AM | 35.1 | 10:59:59 AM
12 | 0 | 1.6 | 10:53:57 AM | 2.5 | 10:54:05 AM | -1 | 10:57:37 AM | 0.5 | 10:57:44 AM | -3.1 | 10:59:48 AM | -0.5 | 10:59:54 AM
Test equipment
Renishaw XL-80
Manufacturer | Renishaw plc
Model | Renishaw XL-80
Serial number | 2NMA84
Calibration date | 1/25/2021 0:00
Certificate number | 2NMA84-210125-00
Calibration organization | Renishaw Inc
Renishaw XC-80
Manufacturer | Renishaw plc
Model | Renishaw XC-80
Serial number | 2YNH13
Calibration date | 1/25/2021 0:00
Certificate number | 2YNH13-210125-00
Calibration organization | Renishaw PLC
AirTemperature
Manufacturer | Renishaw plc
Model | AirTemperature
Serial number | 23J127
Calibration date | 1/25/2021 0:00
Certificate number | 20210125-23J127-00
Calibration organization | Renishaw plc
AirPressure
Manufacturer | Renishaw plc
Model | AirPressure
Serial number | 23J081
Calibration date | 1/25/2021 0:00
Certificate number | 20210125-23J081-00
Calibration organization | Renishaw plc
MaterialTemperature1
Manufacturer | Renishaw plc
Model | MaterialTemperature1
Serial number | 23H984
Calibration date | 1/25/2021 0:00
Certificate number | 20210125-23H984-00
Calibration organization | Renishaw plc
Sensor | Start reading | End reading | Min reading | Max reading
Air temp [°C] | 23.3 | 23.3 | 23.3 | 23.3
Air pressure [mbar] | 974.8 | 974.8 | 974.8 | 975
Air humidity [%RH] | 60 | 60 | 60 | 60
Material temp 1 [°C] | 23.4 | 23.4 | 23.4 | 23.4
Material temp 2 [°C] | Not recorded | Not recorded
Material temp 3 [°C] | Not recorded | Not recorded

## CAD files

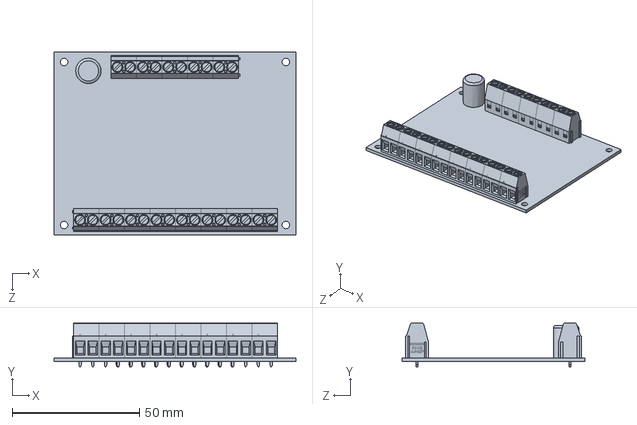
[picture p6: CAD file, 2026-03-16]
Solidworks CAD/Electrical-Box/DST-1R8P-P optocoupler board assembly part.SLDPRT
95.0 x 17.1 x 72.0 mm

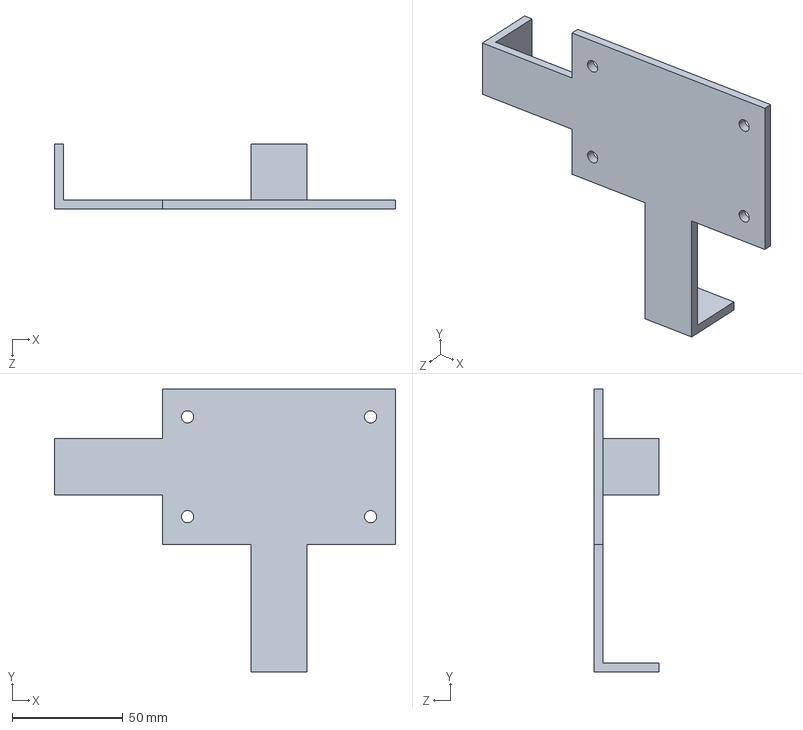
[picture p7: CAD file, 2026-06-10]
3D Printing Files/Electrical Box/Drill and Box Prep Guides/ContactorGuide.STEP
153.8 x 127.5 x 29.4 mm

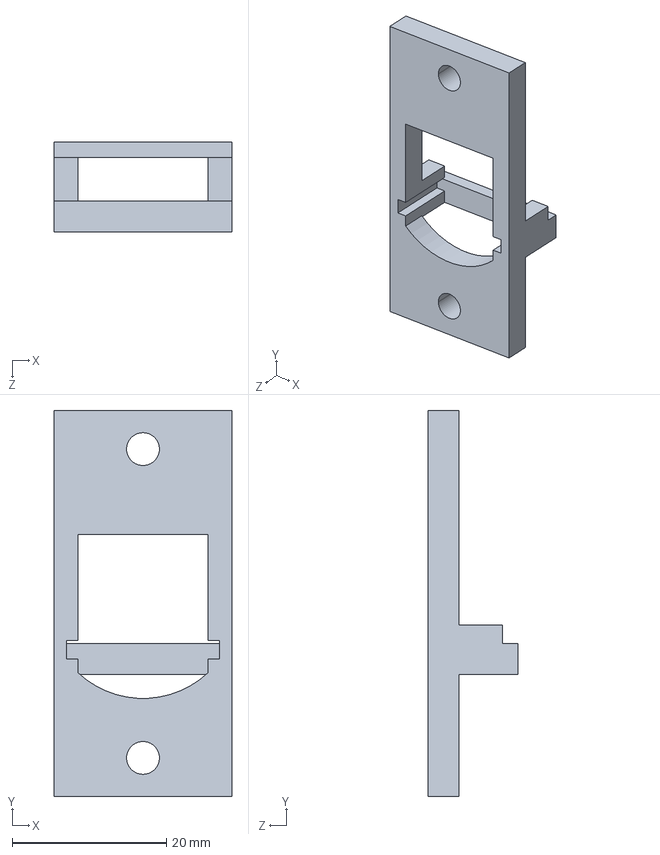
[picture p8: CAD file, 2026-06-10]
3D Printing Files/Electrical Box/Ethernet Conversion/MagJackPlate.STEP
23.0 x 50.0 x 11.6 mm

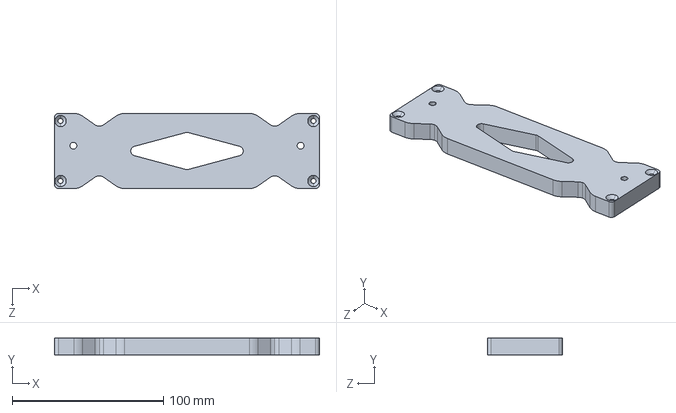
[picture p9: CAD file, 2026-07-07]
3D Printing Files/Electrical Box/PSU Side Mount 3.STEP
175.0 x 11.0 x 49.6 mm

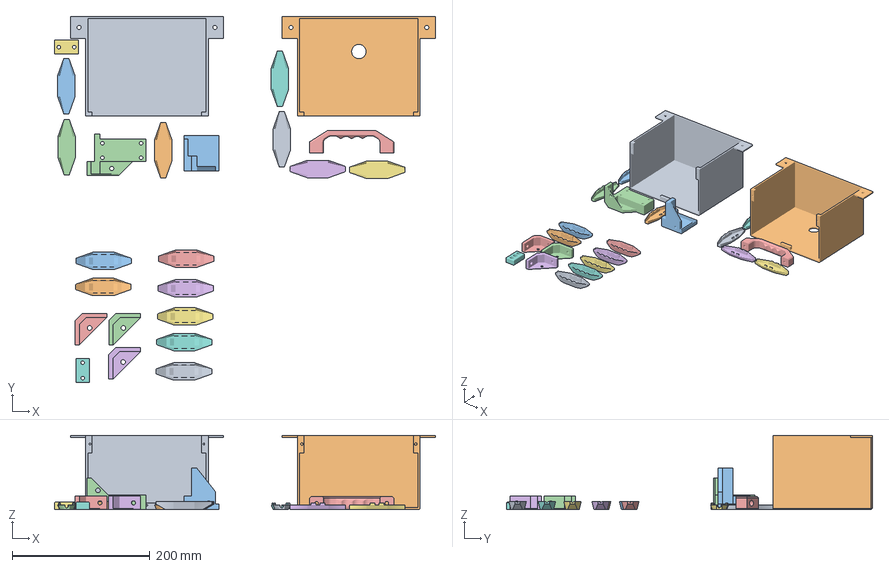
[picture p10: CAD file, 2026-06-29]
3D Printing Files/Enclosure/Enclosure Print Layout.3mf
552.4 x 530.6 x 107.9 mm
Enclosure cover 1 v1.step
Enclosure cover 2 v1.step
Corner Bracket with Magnet Top.STEP
Corner Bracket with Magnet Bottom V2.STEP
CNC Mill Door Handle.STEP
Connector cover top.STEP x 7
Connector cover bottom.STEP x 7
Corner Bracket for Hinge Door.STEP x 3
Magnet Frame Mount.STEP x 2

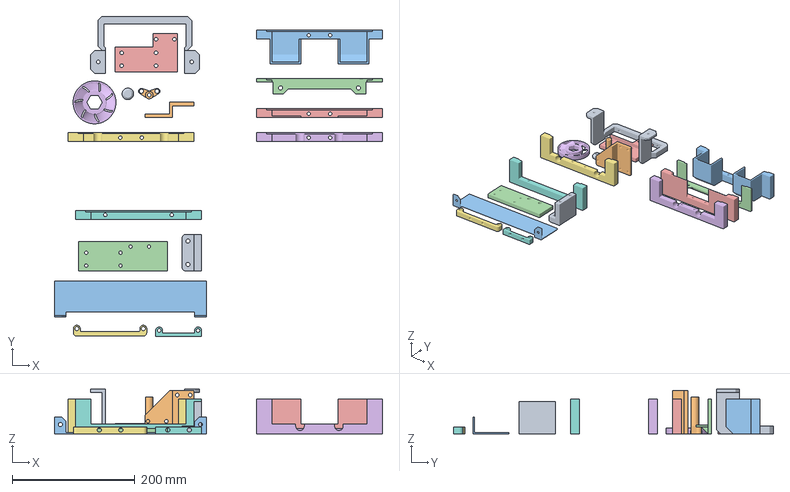
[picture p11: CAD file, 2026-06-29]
3D Printing Files/Machine/Machine Print Layout.3mf
535.0 x 522.6 x 73.2 mm
Z-axis Way Cover Bracing Side.STEP
Z-Axis Limit switch mount.STEP
Y-axis Way Cover Cover motor Side.STEP
X-axis Way Cover Bed Side.STEP
X-axis Way Cover Motor Side.STEP
Y-axis Way Cover Cover Column Side .STEP
Y-axis Way Cover Cover Side.STEP
Z-axis Way Cover Bed Side.STEP
X-axis Way Cover Mount.STEP
Probe holder.STEP
x hard cover.STEP
Y-Axis Limit switch mount.STEP
X-Axis Limit switch mount.STEP
Collet Fan.STEP
Y-axis Way Cover Saddle Side.STEP
Y-axis Way Cover Column Side.STEP
Probe touch plate.STEP

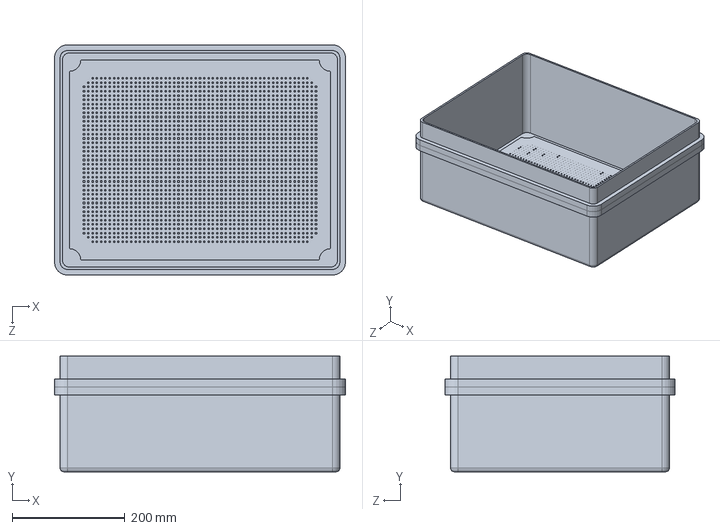
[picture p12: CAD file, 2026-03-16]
Solidworks CAD/Electrical-Box/Electrical Box.SLDPRT
516.0 x 205.0 x 408.0 mm

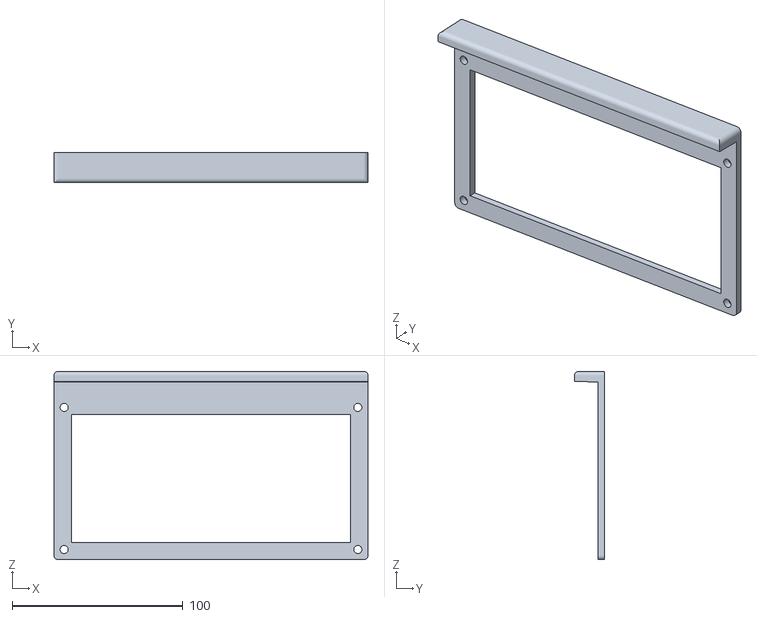
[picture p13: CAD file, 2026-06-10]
3D Printing Files/Electrical Box/Drill and Box Prep Guides/BigJig.STL
184.1 x 17.8 x 110.5

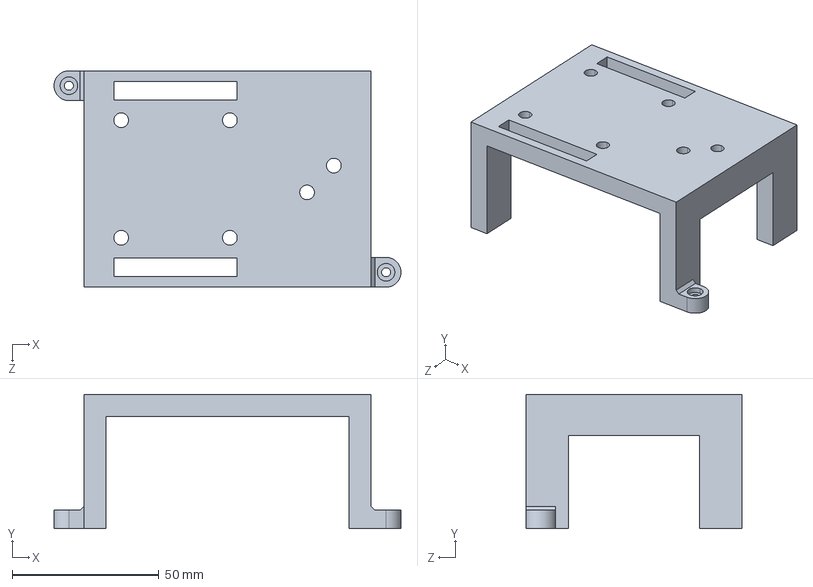
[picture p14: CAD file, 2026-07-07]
3D Printing Files/Electrical Box/OptoMount5.0.STEP
118.1 x 45.7 x 73.7 mm

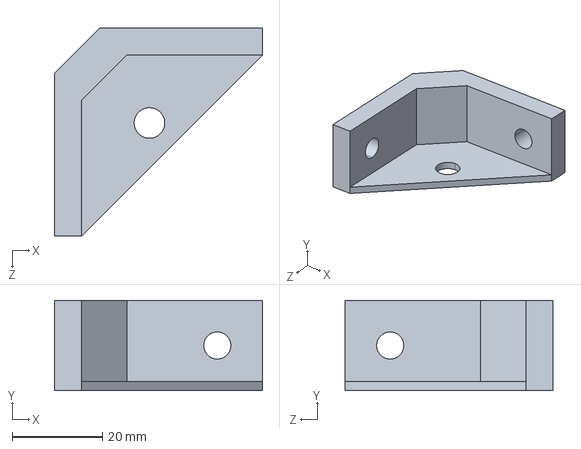
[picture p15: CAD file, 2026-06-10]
3D Printing Files/Enclosure/Corner Bracket for Hinge Door.STEP
46.0 x 20.0 x 46.0 mm

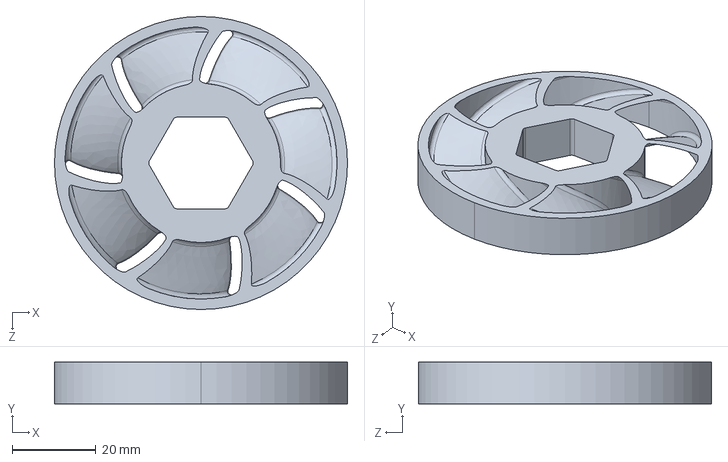
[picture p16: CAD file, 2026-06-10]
3D Printing Files/Machine/Collet Fan.STEP
70.0 x 10.0 x 70.0 mm

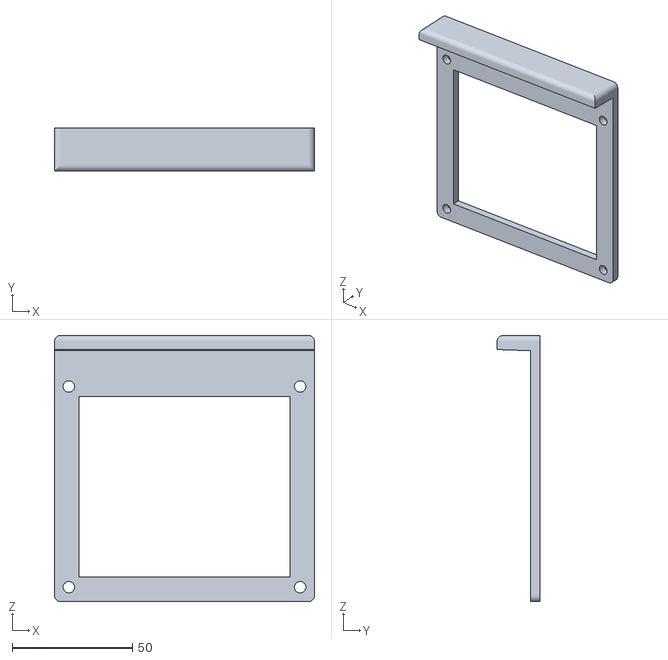
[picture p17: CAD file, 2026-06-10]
3D Printing Files/Electrical Box/Drill and Box Prep Guides/SmallJig.STL
108.0 x 17.8 x 110.5

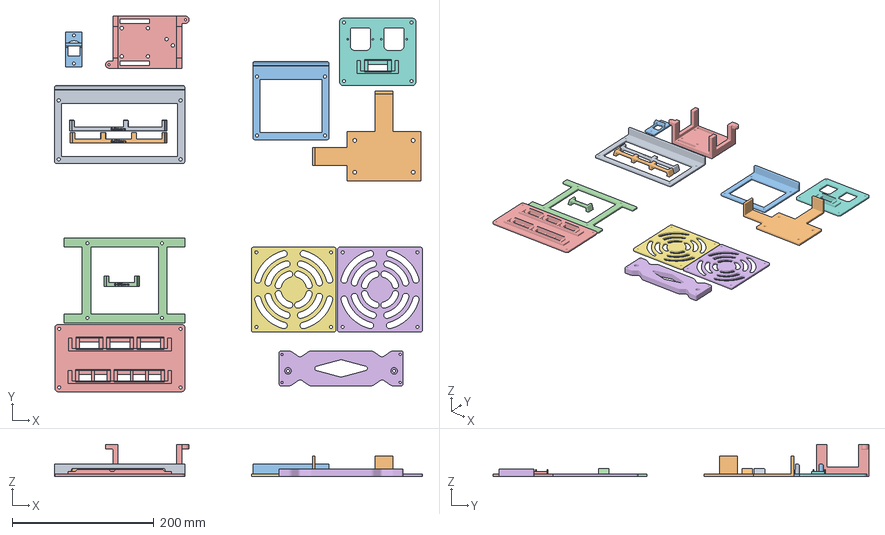
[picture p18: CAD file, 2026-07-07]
3D Printing Files/Electrical Box/Electrical Box 3D Print Layout.3mf
520.1 x 530.9 x 45.7 mm
BigJig.STL
ContactorGuide.STEP
SmallJig.STL
FanHoleGuides.STEP
DoveTailPlateFINAL.STEP
FanGrills.STEP x 2
SmallPlateDoveTail.STEP
3PinDoveTailBracket025TEST.STEP
5PinDoveTailBracket025TEST.STEP
MagJackPlate.STEP
SingleDoveTail.STEP
OptoMount5.0.STEP
PSU Side Mount 3.STEP

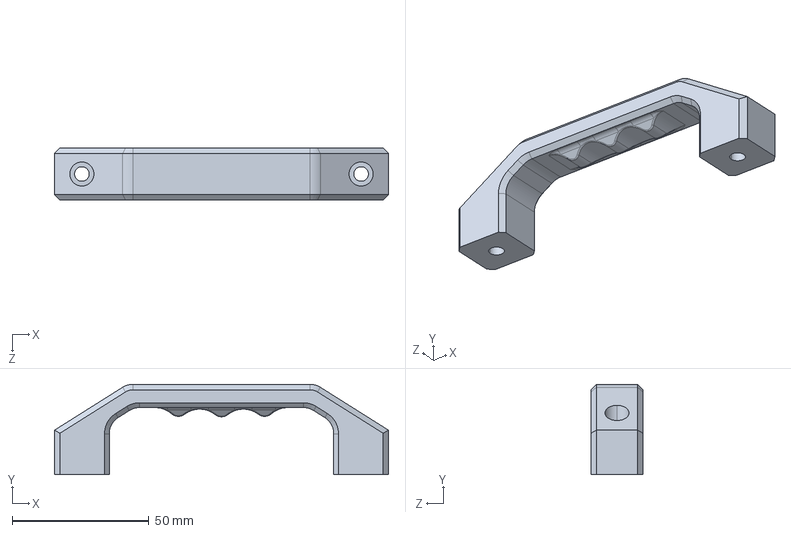
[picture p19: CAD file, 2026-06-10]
3D Printing Files/Enclosure/CNC Mill Door Handle.STEP
122.0 x 33.0 x 19.0 mm

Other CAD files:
Solidworks CAD/Electrical-Box/Logi Level Converter.SLDASM
Solidworks CAD/Electrical-Box/EBOX.SLDASM
3D Printing Files/Machine/Probe touch plate.STEP
3D Printing Files/Electrical Box/3PinDoveTailBracket025TEST.STEP
3D Printing Files/Electrical Box/5PinDoveTailBracket025TEST.STEP
3D Printing Files/Electrical Box/DoveTailPlateFINAL.STEP
3D Printing Files/Electrical Box/Drill and Box Prep Guides/FanHoleGuides.STEP
3D Printing Files/Electrical Box/FanGrills.STEP
3D Printing Files/Electrical Box/SingleDoveTail.STEP
3D Printing Files/Electrical Box/SmallPlateDoveTail.STEP
3D Printing Files/Enclosure/Connector cover bottom.STEP
3D Printing Files/Enclosure/Connector cover top.STEP
3D Printing Files/Enclosure/Corner Bracket with Magnet Bottom V2.STEP
3D Printing Files/Enclosure/Corner Bracket with Magnet Top.STEP
3D Printing Files/Enclosure/Enclosure cover 1 v1.step
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

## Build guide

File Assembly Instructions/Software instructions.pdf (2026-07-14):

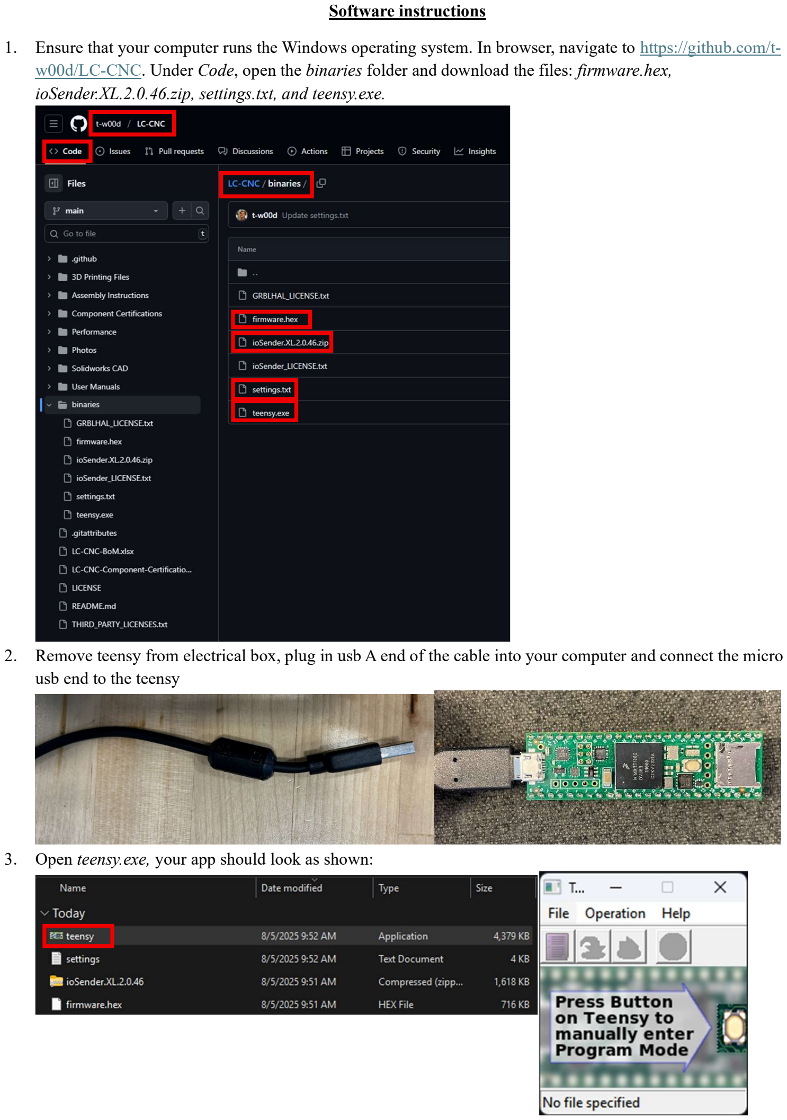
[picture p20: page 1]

Software instructions

1. Ensure that your computer runs the Windows operating system. In browser, navigate to https://github.com/tw00d/LC-CNC. Under Code, open the binaries folder and download the files: firmware.hex, ioSender.XL.2.0.46.zip, settings.txt, and teensy.exe.
2. Remove teensy from electrical box, plug in usb A end of the cable into your computer and connect the micro usb end to the teensy

### 3. Open teensy.exe, your app should look as shown:

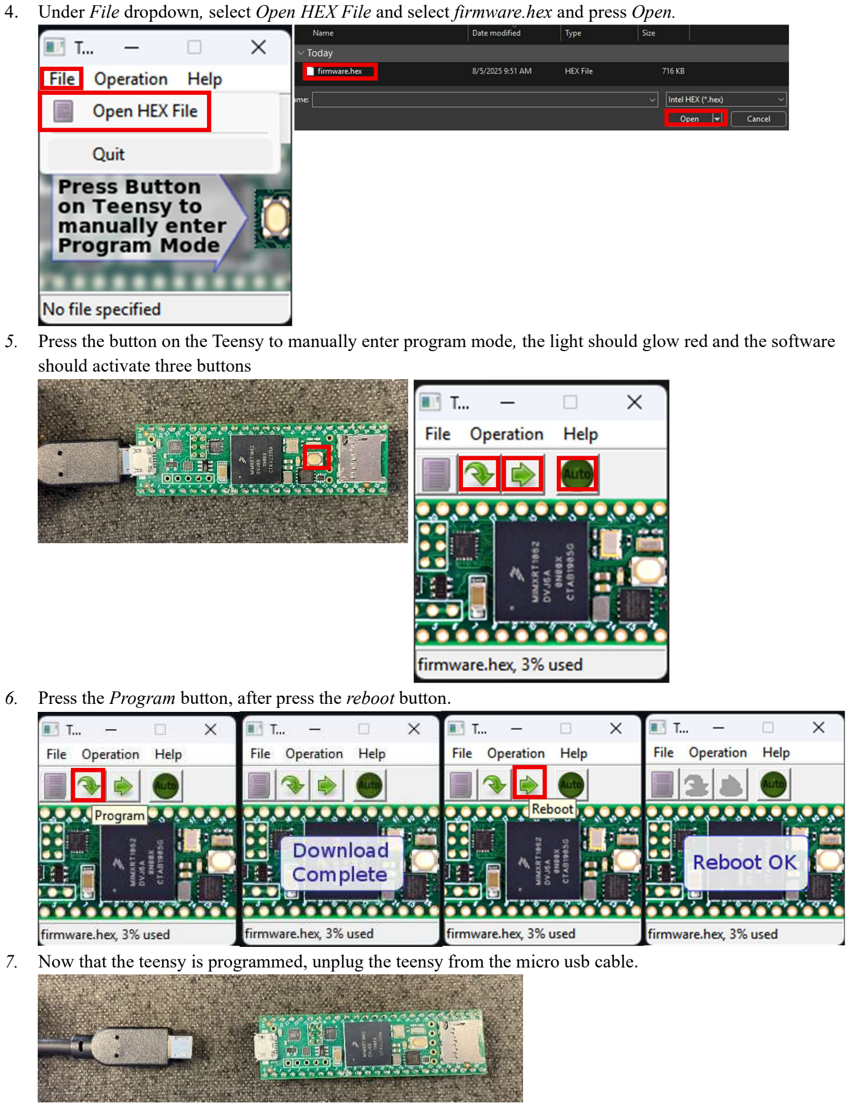
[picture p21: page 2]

4. Under File dropdown, select Open HEX File and select firmware.hex and press Open.
5. Press the button on the Teensy to manually enter program mode, the light should glow red and the software should activate three buttons
6. Press the Program button, after press the reboot button.
7. Now that the teensy is programmed, unplug the teensy from the micro usb cable.

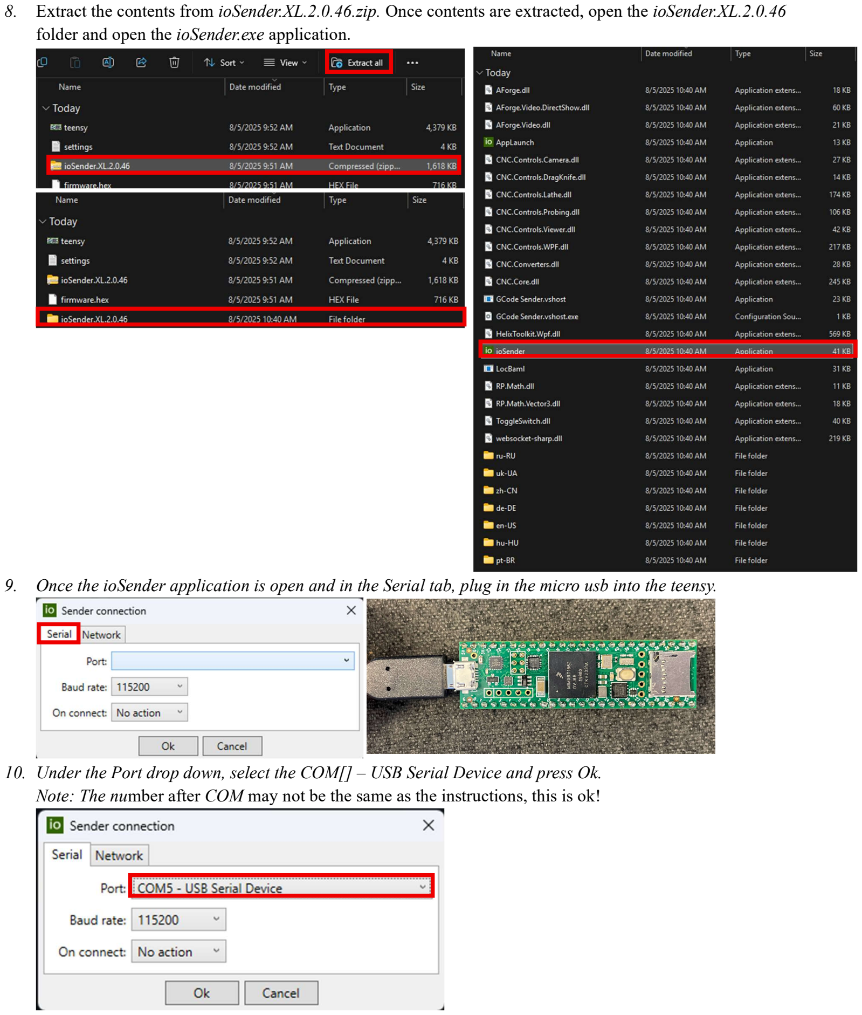
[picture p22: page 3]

8. Extract the contents from ioSender.XL.2.0.46.zip. Once contents are extracted, open the ioSender.XL.2.0.46 folder and open the ioSender.exe application.
9. Once the ioSender application is open and in the Serial tab, plug in the micro usb into the teensy.
10. Under the Port drop down, select the COM[] – USB Serial Device and press Ok. Note: The number after COM may not be the same as the instructions, this is ok!

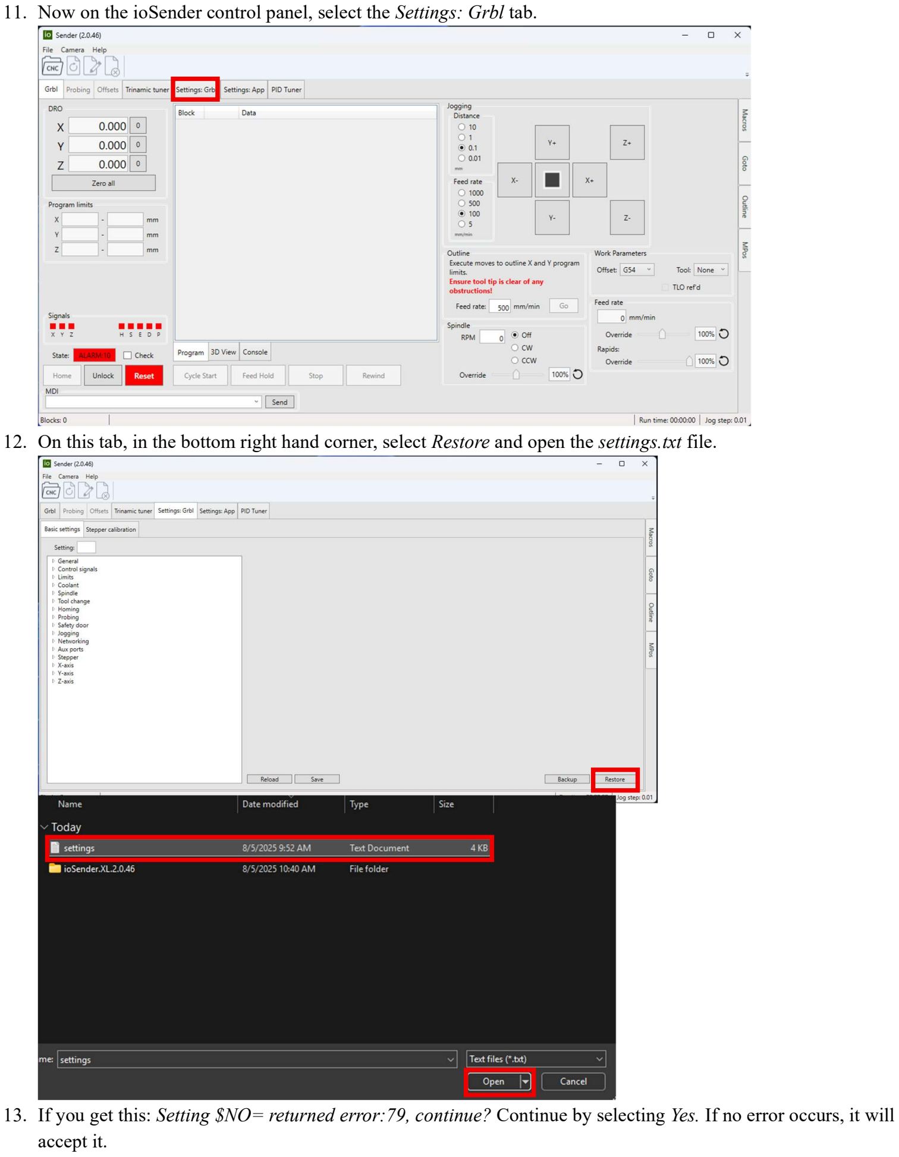
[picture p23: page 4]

11. Now on the ioSender control panel, select the Settings: Grbl tab.
12. On this tab, in the bottom right hand corner, select Restore and open the settings.txt file.
13. If you get this: Setting $NO= returned error:79, continue? Continue by selecting Yes. If no error occurs, it will accept it.

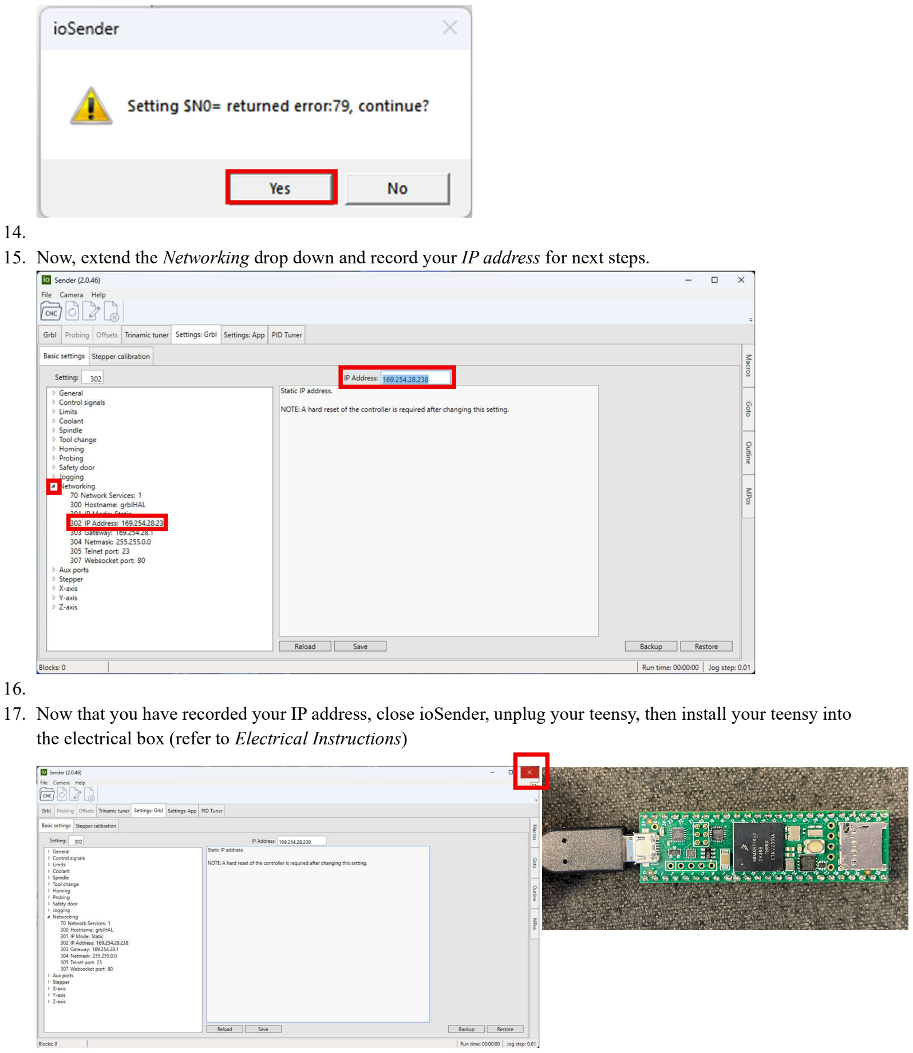
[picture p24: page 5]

14.
15. Now, extend the Networking drop down and record your IP address for next steps.

16.
17. Now that you have recorded your IP address, close ioSender, unplug your teensy, then install your teensy into the electrical box (refer to Electrical Instructions)

18. Ensure your ethernet cable is plugged into the teensy and your computer.

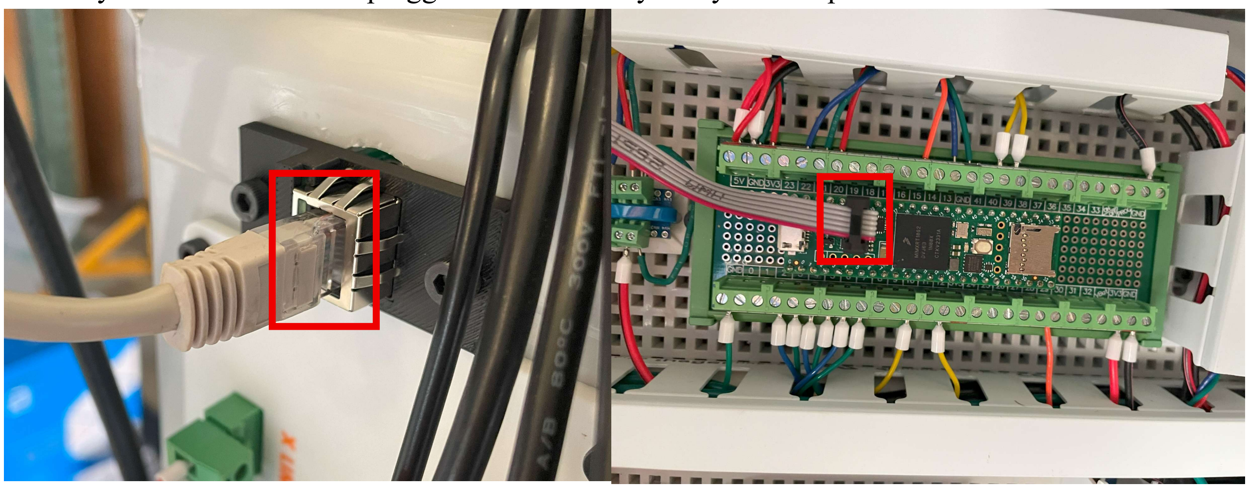
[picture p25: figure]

19. Open ioSender and navigate to Settings: Grbl and extend the Network drop down and ensure your IP address is the same as the one you recorded earlier.

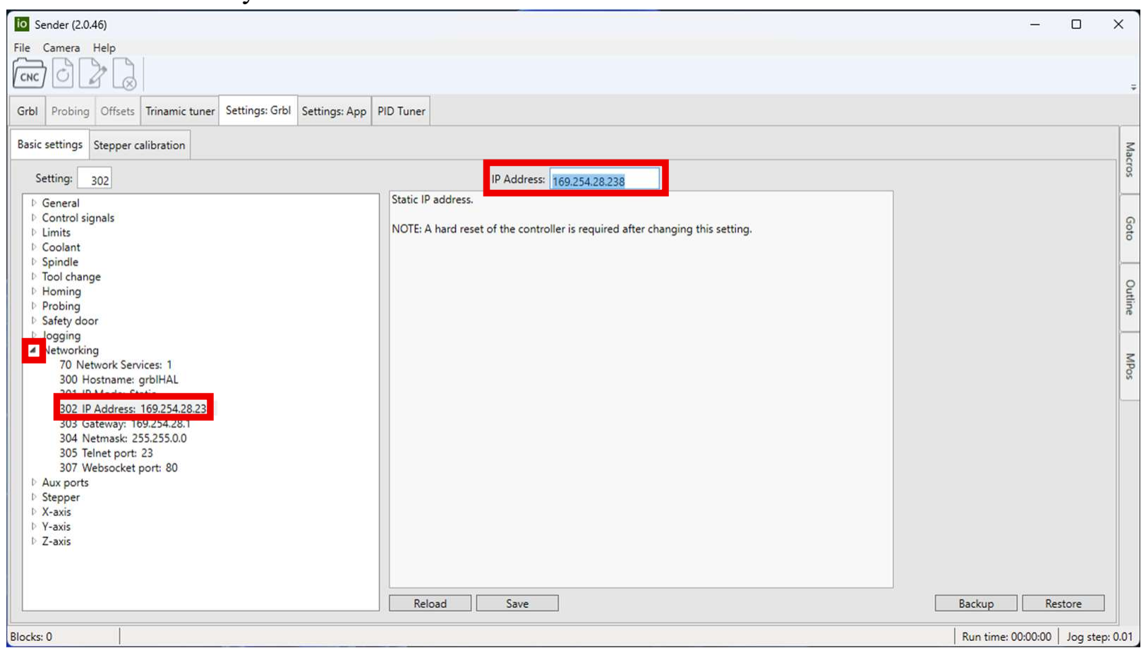
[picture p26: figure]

20. The Teensy 4.1 is now set up to run G-code with the proper settings specific to this machine.
21. Next, we will program the VFD with the proper settings for our electrical configuration. Begin by plugging the IEC cable to the VFD port on the small connector plate. Switch on the receptacle.

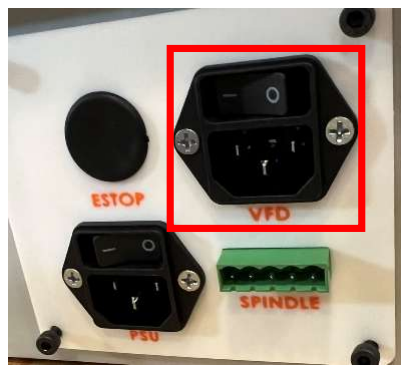
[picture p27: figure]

22. Follow the instructions in this video to learn how to change VFD settings. Do not use the settings provided in the video. After learning how to adjust the settings using the “Set” button, input the following settings.
Note: If pressing the “Set” button doesn’t change the display, press the “Stop” button and try again. Cycle VFD power after settings have been changed.

Video: https://youtu.be/J6nqaAiBo0M?si=FlONAb2tYMn_0HIu&t=230

F001: 1
F002: 1
F014: 6
F044: 01
F070: 01
F140: 2.2
F142: 8.6
F170: 02
F171: 03

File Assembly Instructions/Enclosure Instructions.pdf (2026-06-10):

FIND ALL OF THESE ITEM DESCRIPTIONS IN “LC-CNC-BoM” FOR ITEM LINKS

Description | Qty
1 | M5x12 mm bolts (100 pack) | 1
2* | M5 hex nut (100 pack) | 1
3 | M3x10mm bolts (100 pack) | 1
4* | Magnets (30 pack) | 30
5 | 20-2020 LENGTH: 596.6 millimeters | 8
6 | 20-2020 LENGTH: 636.6 millimeters | 4
7 | 20-2020 LENGTH: 593.6 millimeters | 2
8 | 20-2020 LENGTH: 553.6 millimeters | 2
9* | 14157 Economy Gasket LENGTH: 8 meters | 1
10 | Hinges | 2
11 | T-Nuts (10 pack) | 10
12 | L Connector Bracket (10 pack) | 2
13* | Polycarbonate sheet (24x24x1/8”) | 2
14* | Loctite-Blue | 1
15 | Limit Switches | 1
16 Cord grip
| 3D PRINTS
17 | CNC Mill Door Handle.STEP | 1
18 | Corner Bracket for Hinge Door.STEP | 3
19 | Corner Bracket with Magnet Bottom V2.STEP | 1
20 | Corner Bracket with Magnet Top.STEP | 1
21 | Enclosure cover 1 v1.step | 1
22 | Enclosure cover 2 v1.step | 1
23 | Magnet Frame Mount.STEP | 2
24* | Connector cover bottom.STEP | 7
25* | Connector cover top.STEP | 7
| Custom Polycarbonate Sheets (IF NOT SENT THESE, ORDER FIVE 24x24x1/8” SHEETS AND CUT TO SPECIFICATION)
26* | Polycarbonate top panel.dxf (File in 3D printing files>Enclosure, then custom cut 24x24x1/8” ) | 1
27* | Polycarbonate back panel (Refer to step 7, drill two 1” holes into lower corners of 24x24x1/8”) | 1
28* | Polycarbonate door panel (Trim polycarb sheet to 22.2x22.2x1/8”) | 1
*Not referenced

1. Gather M5*12 bolts and t-nuts, then attach these to the corner brackets. Make sure these bolts are loosely tightened.

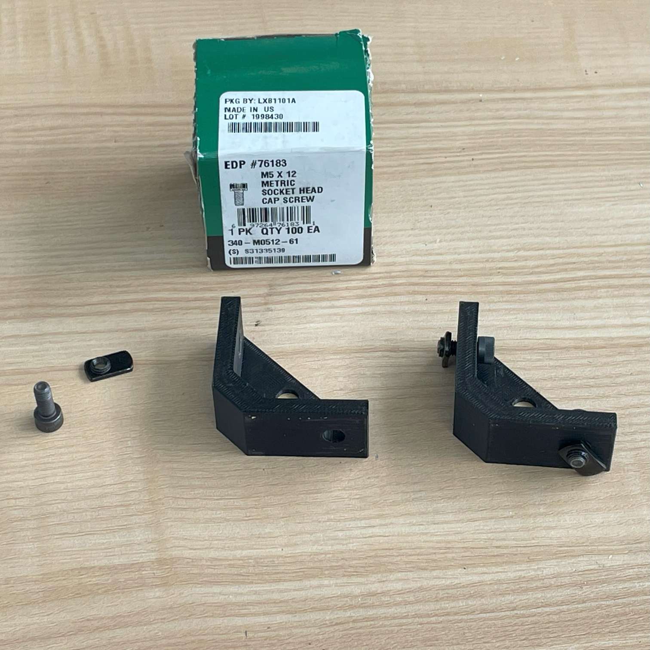
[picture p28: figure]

2. Gather your magnets, magnet frame mount, bottom corner bracket, and top corner bracket. Apply super glue to the magnets and holes as shown. Make sure the magnet frame mount attracts to both top and bottom corner brackets.

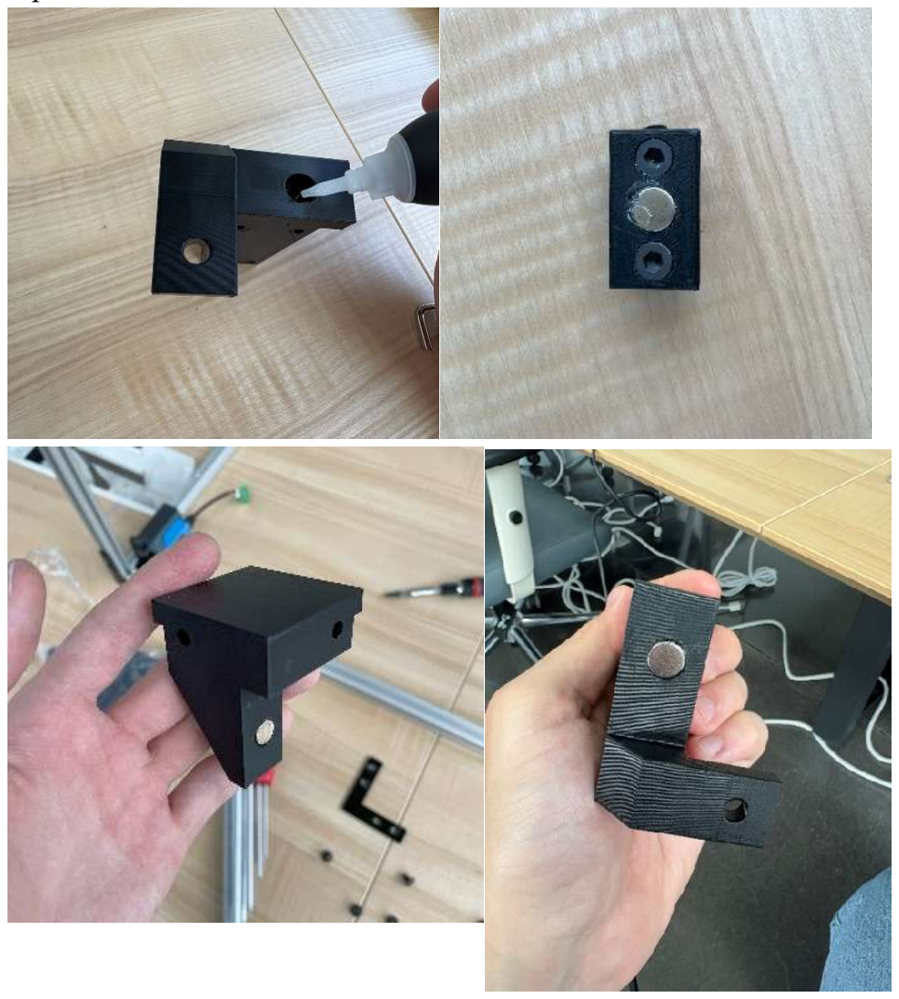
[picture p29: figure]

3. Take the 596mm extrusions and slide them into the corner brackets as such.

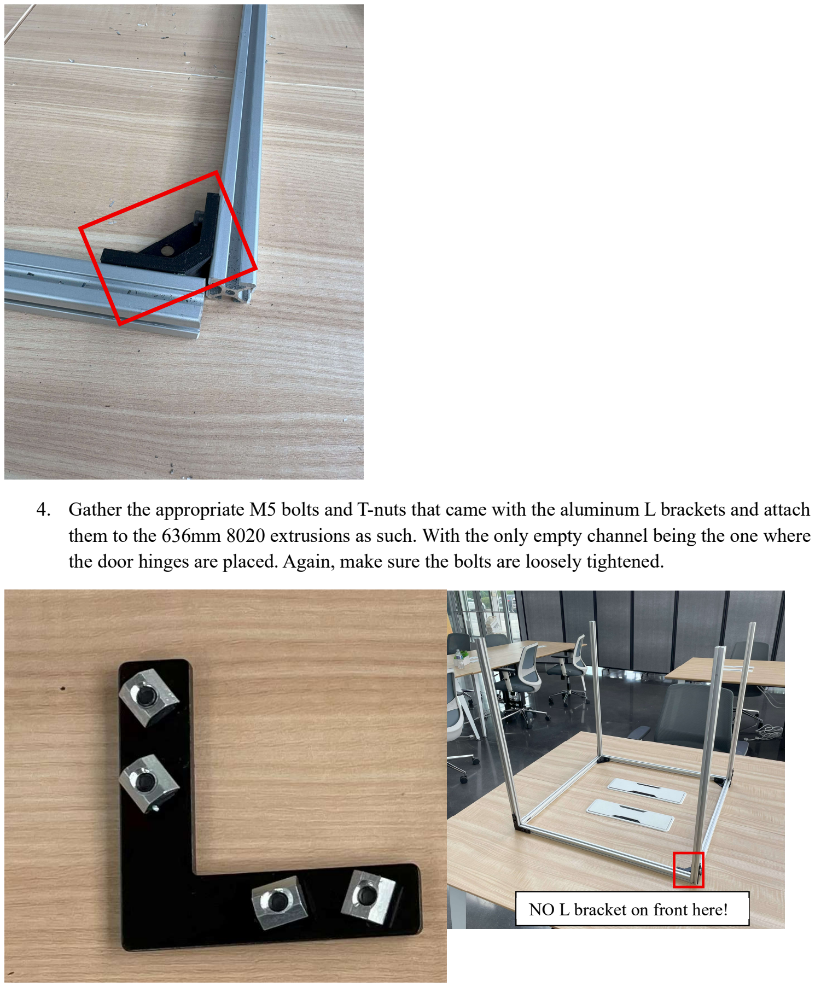
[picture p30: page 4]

4. Gather the appropriate M5 bolts and T-nuts that came with the aluminum L brackets and attach them to the 636mm 8020 extrusions as such. With the only empty channel being the one where the door hinges are placed. Again, make sure the bolts are loosely tightened.

NO L bracket on front here!

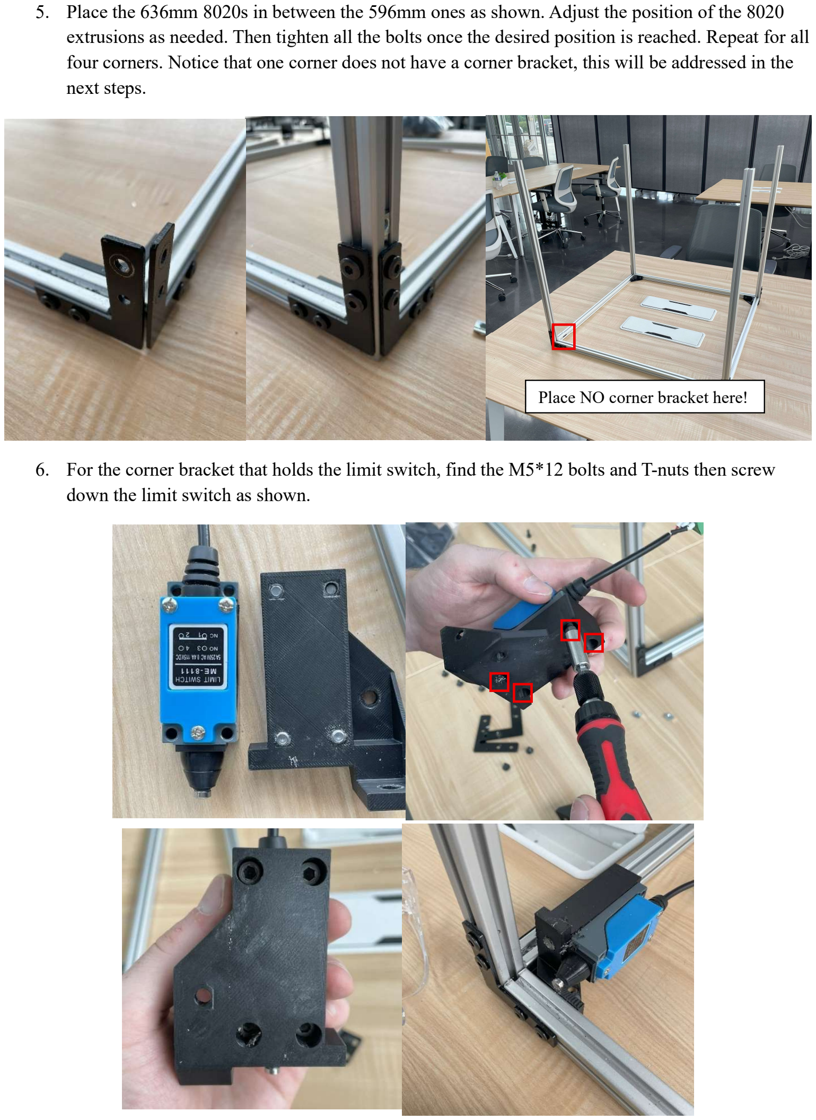
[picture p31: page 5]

5. Place the 636mm 8020s in between the 596mm ones as shown. Adjust the position of the 8020 extrusions as needed. Then tighten all the bolts once the desired position is reached. Repeat for all four corners. Notice that one corner does not have a corner bracket, this will be addressed in the next steps.
6. For the corner bracket that holds the limit switch, find the M5*12 bolts and T-nuts then screw down the limit switch as shown.

Place NO corner bracket here!

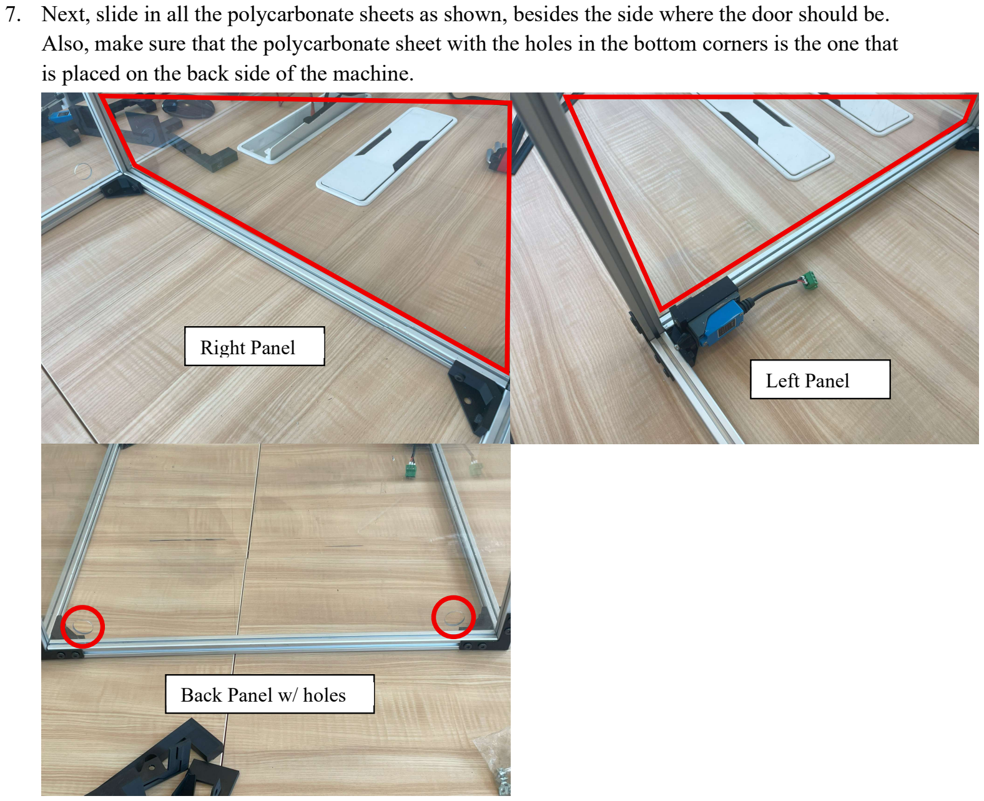
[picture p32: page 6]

7. Next, slide in all the polycarbonate sheets as shown, besides the side where the door should be. Also, make sure that the polycarbonate sheet with the holes in the bottom corners is the one that is placed on the back side of the machine.

Back Panel w/ holes

Left Panel

Right Panel

8. With the panels in place, prepare aluminum L brackets with its M5 bolts and T-nuts that came with them and attach them to all four corners as such.

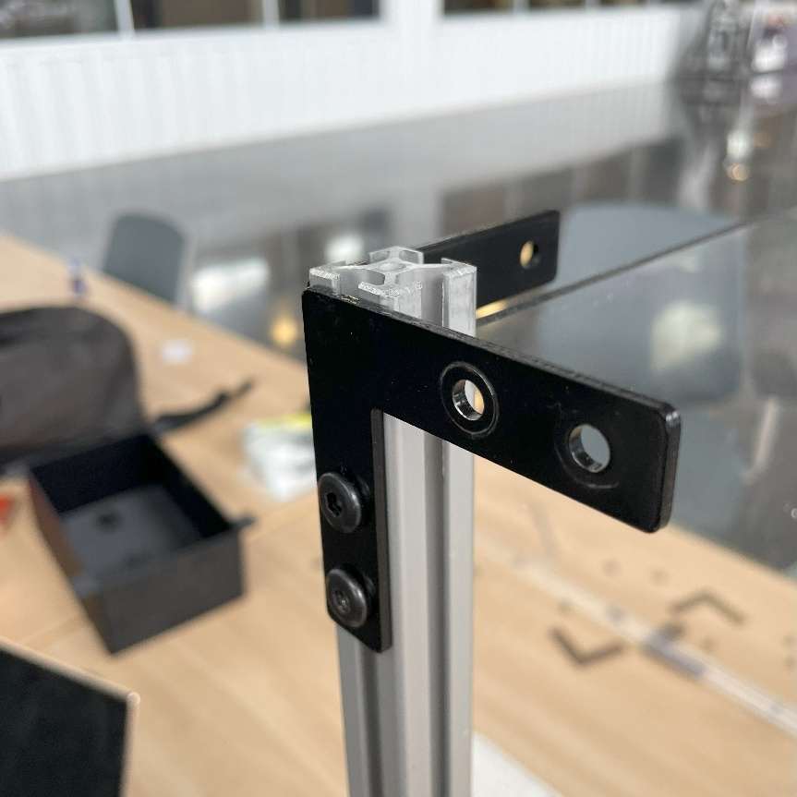
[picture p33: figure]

9. With the L brackets in place on each corner, grab the custom cut polycarbonate top panel, four 596mm extrusions, and four L brackets with its corresponding M5 bolts and nuts. Connect three extrusions together with two L brackets and slide in the top panel to keep the corners square. Tighten bolts. Slide in two T nuts into the large cutout corner. Make sure the cutout corner is in the bottom left corner.

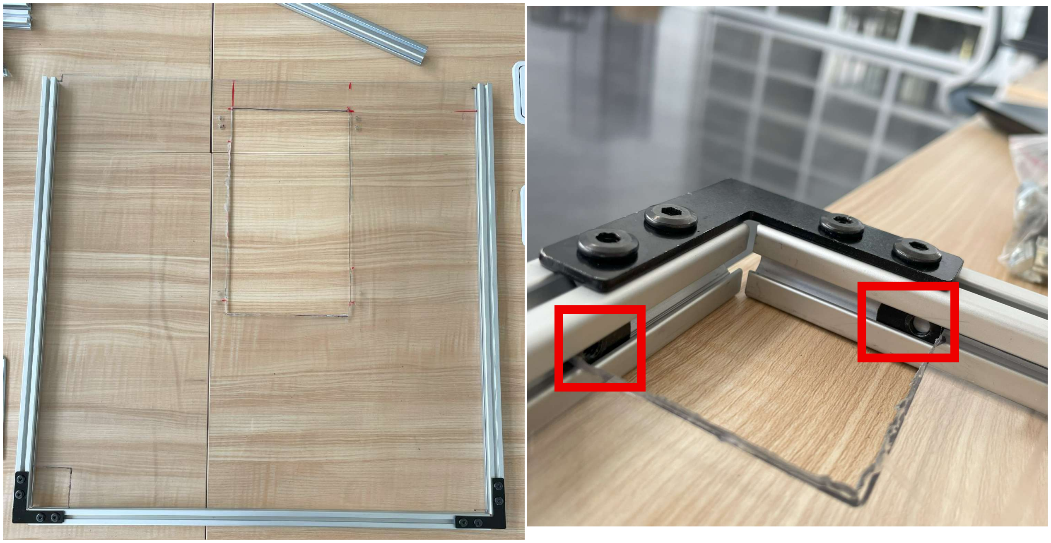
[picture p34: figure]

10. Attach the last 596mm extrusion as shown. Tighten bolts. Insert four T nuts, two on each end of all four extrusions, oriented where the L brackets on each corner of the frame can grab onto the top panel frame.

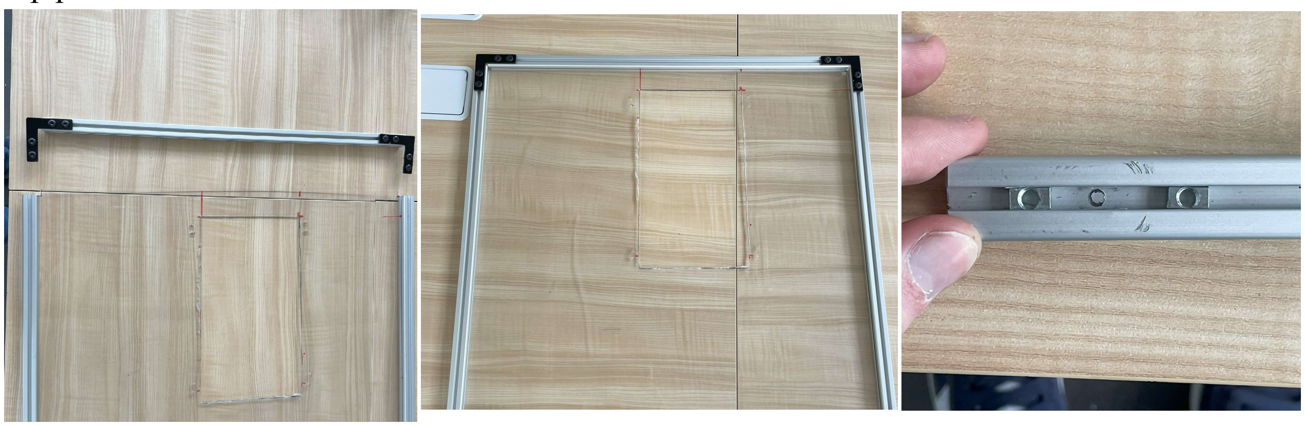
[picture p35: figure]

11. With T nuts in place, slide entire top panel frame into each corner of the frame and mount with corresponding M5 bolts into the inserted T nuts. Ensure the large corner cutout is above the safety switch. Tighten bolts. Place the top corner bracket into the large corner cutout and ensure the magnet is inside the frame and facing the same direction as the limit switch underneath it.

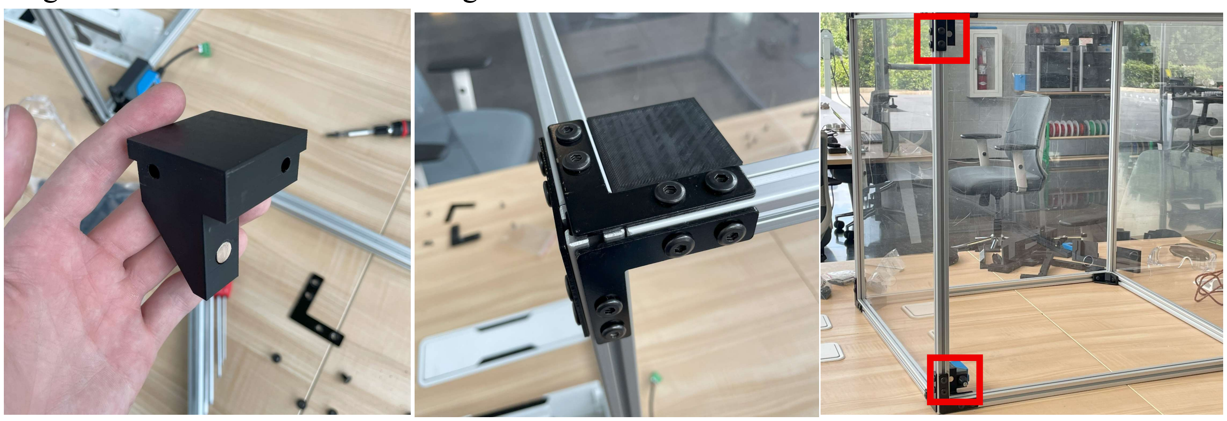
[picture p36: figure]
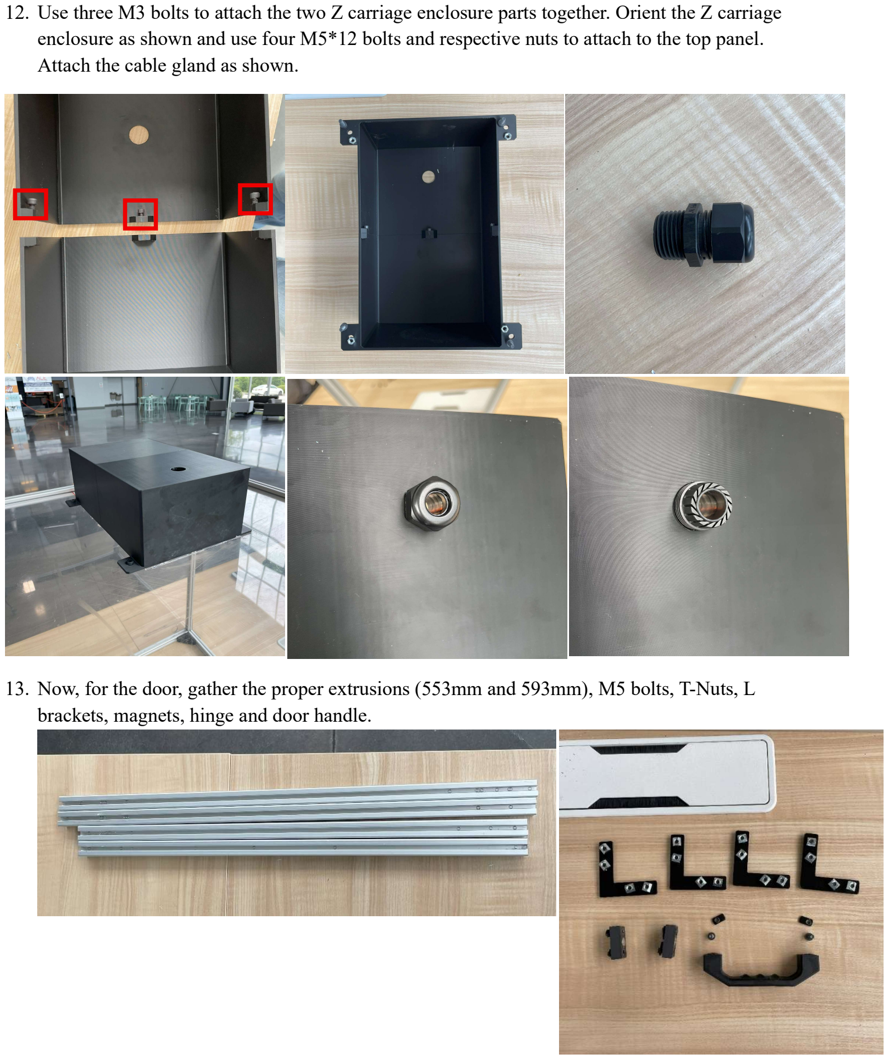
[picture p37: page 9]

12. Use three M3 bolts to attach the two Z carriage enclosure parts together. Orient the Z carriage enclosure as shown and use four M5*12 bolts and respective nuts to attach to the top panel. Attach the cable gland as shown.
13. Now, for the door, gather the proper extrusions (553mm and 593mm), M5 bolts, T-Nuts, L brackets, magnets, hinge and door handle.

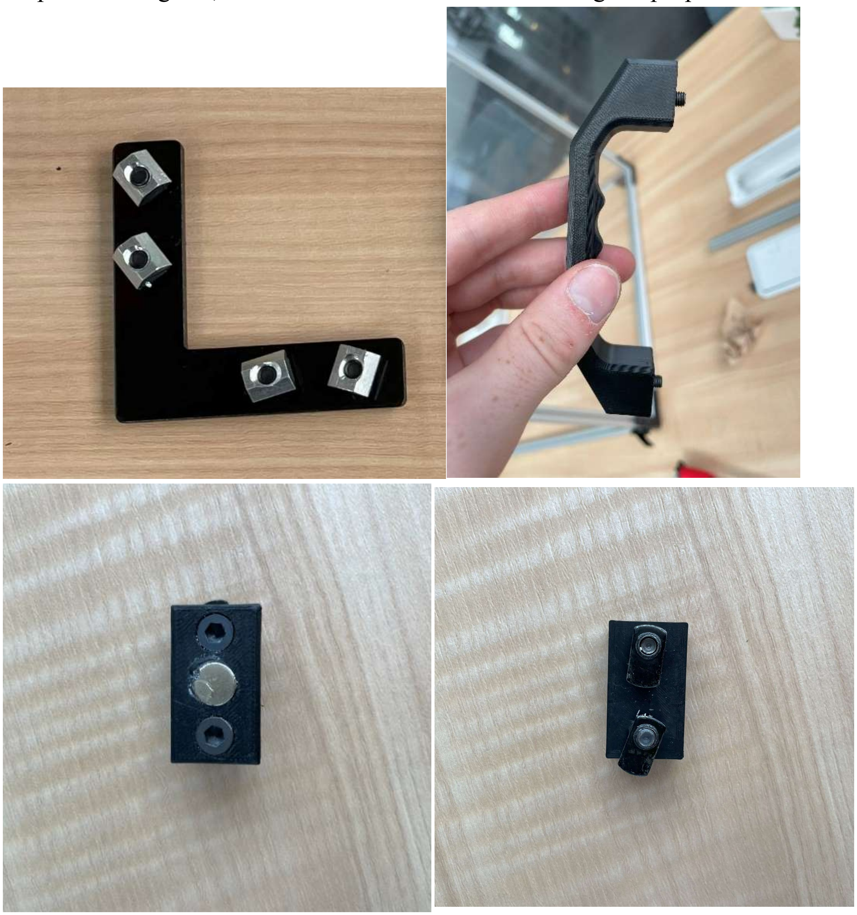
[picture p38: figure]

14. Prepare the magnets, L brackets and door handle attaching the proper bolts and T-nuts as shown.

15. Slide the door handle into the left 553mm extrusion as shown, then tighten it down to the middle of that extrusion.

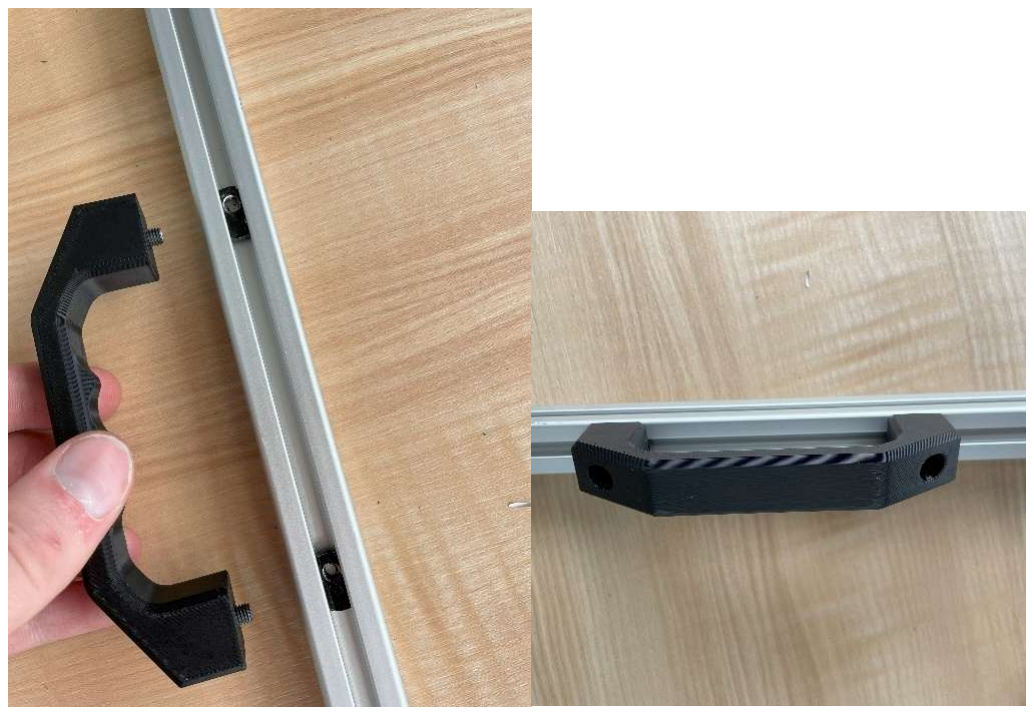
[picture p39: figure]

16. Then take your magnets and L brackets, attach them to the 553mm 8020 with the door handle and loosely secure these as shown.

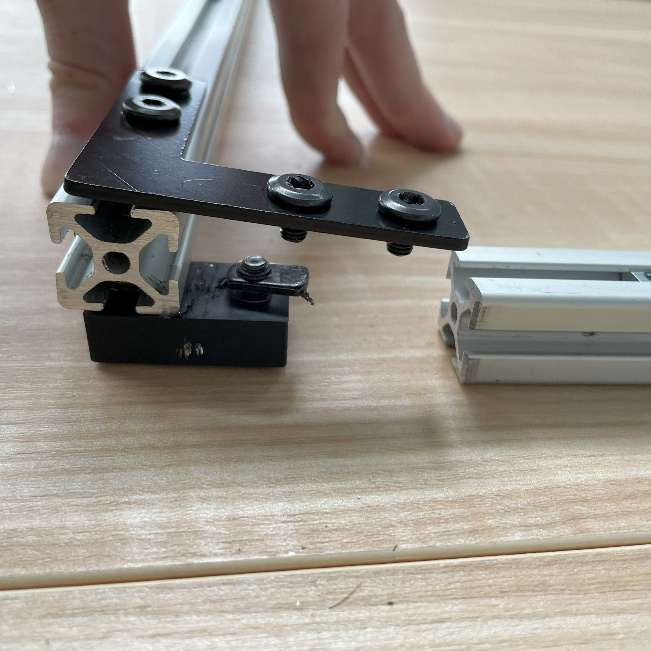
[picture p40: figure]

17. Now slide your 593mm extrusion in, with the 553mm extrusion fitted in between the two as shown and tighten down your brackets and magnets.

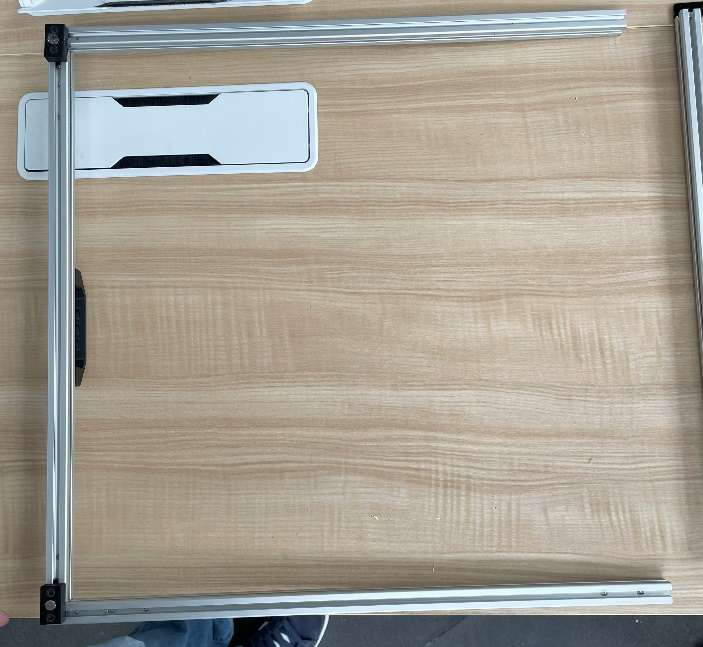
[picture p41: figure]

18. Slide in the front panel 22.2x22.2x1/8” polycarbonate sheet and attach the final L brackets to the opposite end of your door frame with the brackets facing inside the enclosure as shown.

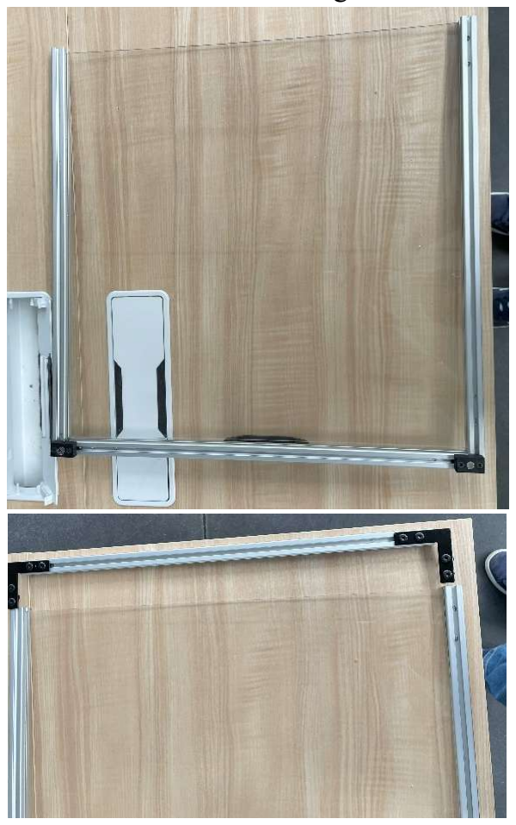
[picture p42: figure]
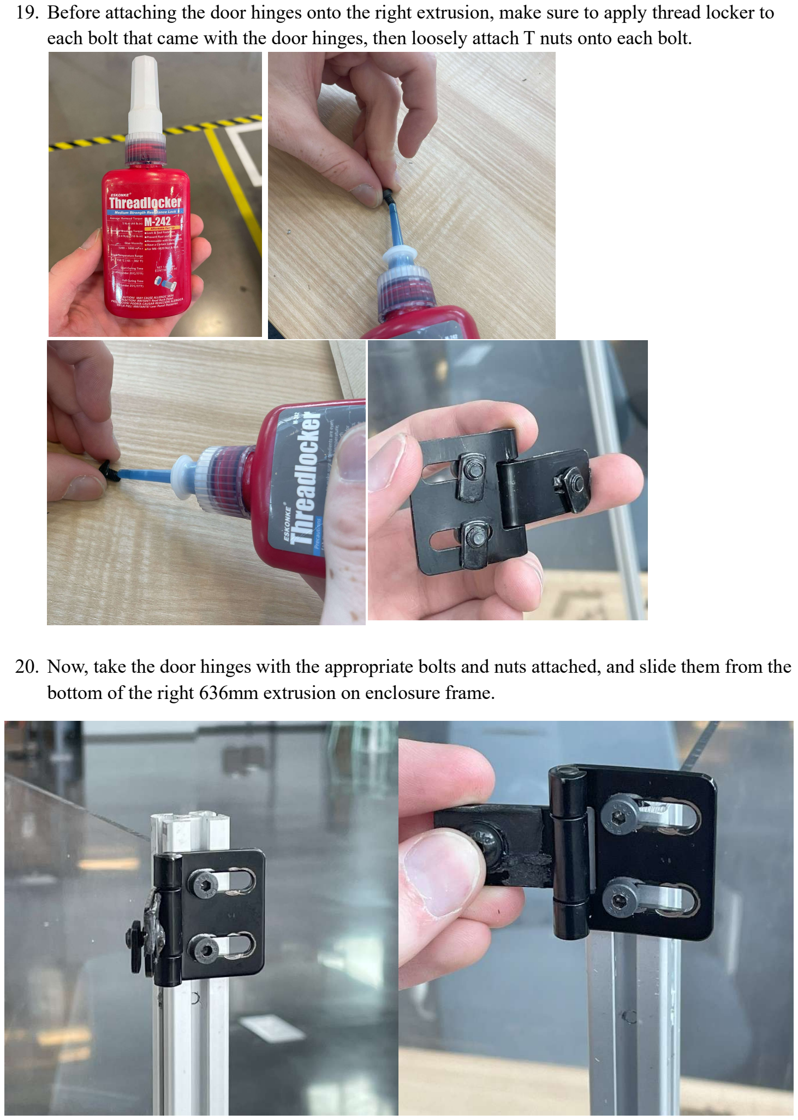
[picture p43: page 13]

19. Before attaching the door hinges onto the right extrusion, make sure to apply thread locker to each bolt that came with the door hinges, then loosely attach T nuts onto each bolt.
20. Now, take the door hinges with the appropriate bolts and nuts attached, and slide them from the bottom of the right 636mm extrusion on enclosure frame.

21. Adjust the position of the hinges to bias the position of the door towards the top of the enclosure, leaving a larger gap at the bottom. When you tighten the bolts for the hinges down, the gaps at the top and bottom should be a similar distance.

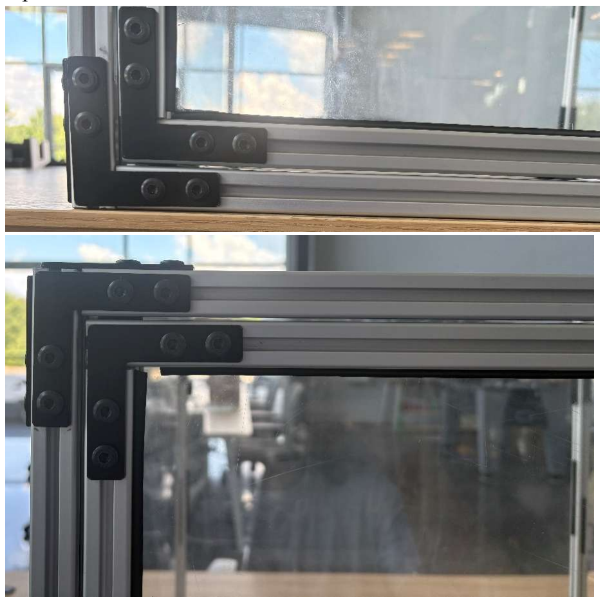
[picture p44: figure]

22. Finally, tighten the hinges to the door as shown. (when testing the door hinge, it may scrape the bottom extrusion, this will most likely be solved when all four corners of the enclosure are mounted on the table.)

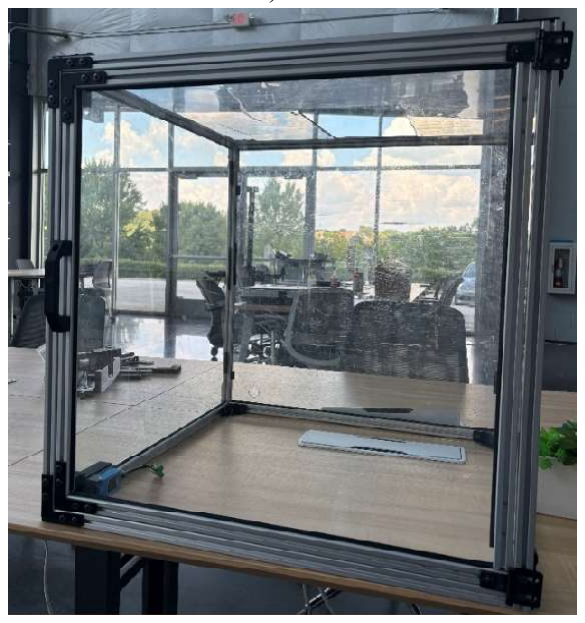
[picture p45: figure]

23. Take the enclosure and place on your table where it should be located with respect to your machine. Mark all four mounting holes on the table where we will need to drill through.

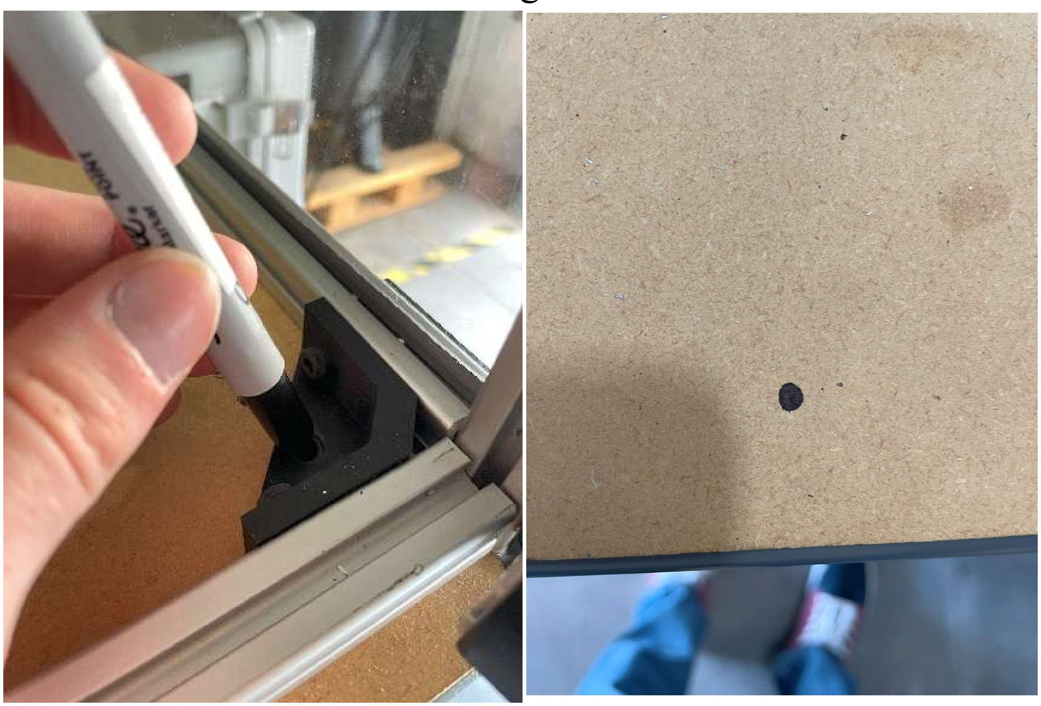
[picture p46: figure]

24. Drill through the table with a H 0.266” drill bit and find four 1/4-20 bolts of appropriate length for your table and corresponding nuts to mount the enclosure on the table.

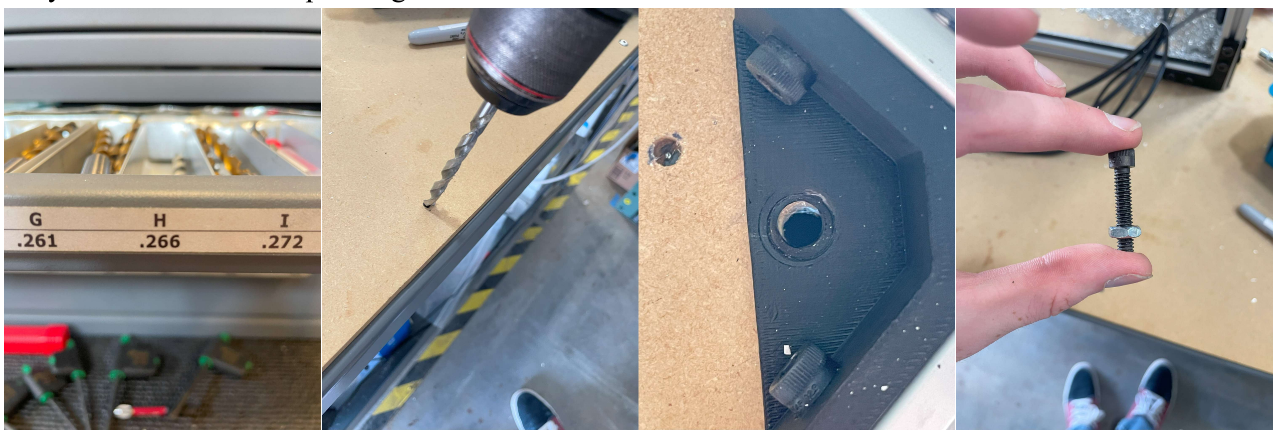
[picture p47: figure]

25. With milling machine in its desired location, place the enclosure over the machine and use a 3/16” Allen wrench to tighten the bolts and corresponding nuts.

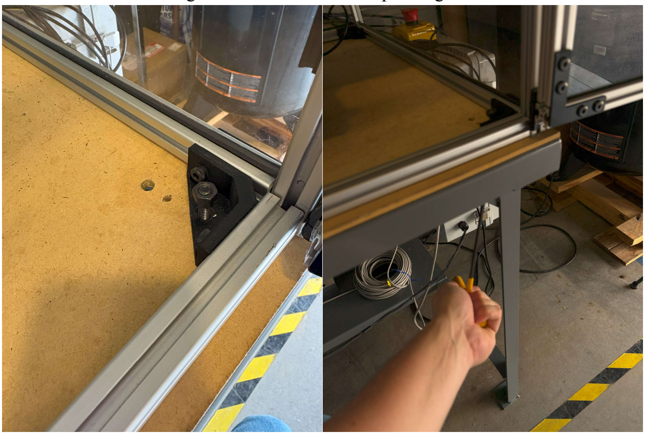
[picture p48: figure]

26. Route your spindle wire through the top of the enclosure as shown. Make sure to put on the cap over the wire to properly hold the cable.

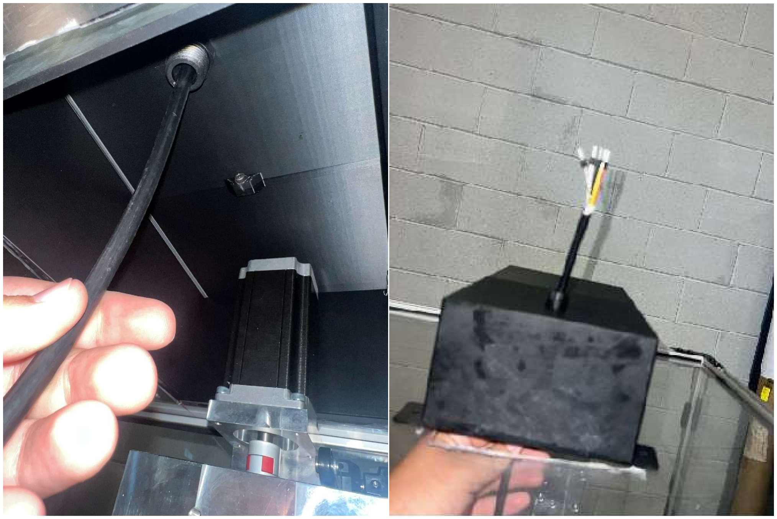
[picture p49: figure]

27. Route all wires for the milling machine through the holes for in the rear panel.

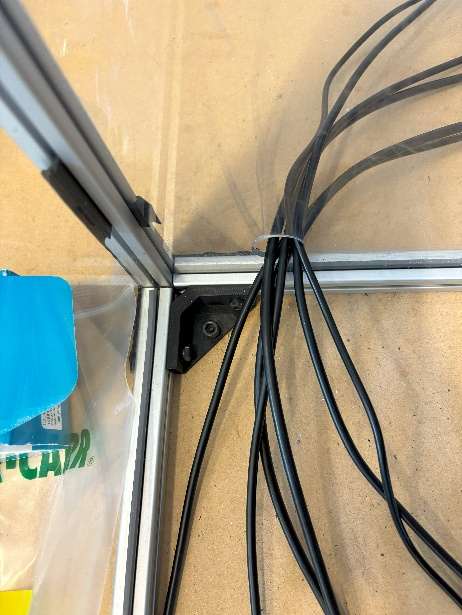
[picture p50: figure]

28. If you find the door still scrapes the bottom extrusion for the enclosure as it opens and closes, readjusting the hinges to bias the door towards the top of the enclosure should give enough room for the door to open and close smoothly. Make sure to reapply thread locker to the hinge bolts after readjustment.
29. If the electrical box is built and wires have been run into the enclosure, connector covers can be used to protect connectors from loose chips and other debris. Simply place the connection in one half of a connector cover pair, place the other half over the top and press until the plastic snaps into place.

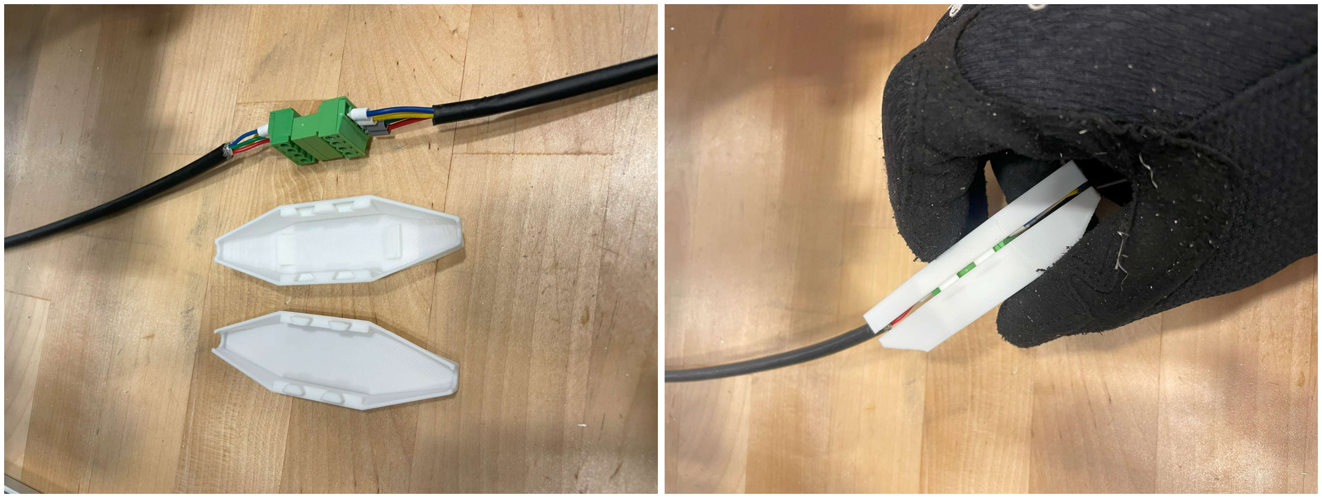
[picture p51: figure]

This cover can be undone by separating the halves.

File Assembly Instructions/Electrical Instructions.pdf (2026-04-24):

Electrical Box Instructions

Item number | Description | Qty
| Electrical Box Soldering Iron Soldering Clips Weicon Automatic Wire Stripper Klein Ferrule Crimp Tool Manual Wire Stripper / Cutter Heat Gun Metric Allen Key Set Small Front Connector Plate Large Front Connector Plate Variable Frequency Drive (VFD) 48V – 12V Step Down Converter Emergency Stop 120 mm Fans 16 AWG Stranded Wire Assortment Heat Shrink Assortment Limit Switches 4-Pin Female and Male Terminal Blocks (Provided with each Stepper Motor) 3-Pin Female and Male Terminal Blocks 5-Pin Female and Male Terminal Blocks DM556 Motor Drivers 2-Core Shielded Cable 4-Core Shielded Cable

Spindle Cable
Crimp Connector Assortment Teensy 4.1 Breakout Board
Teensy 4.1
Power Supply (PSU) Mount
22 AWG Red and Black Stranded Wire Grounding Bus Bar
IEC Cable
IEC Receptacle
#6 Screws

3D Touch Probe
3D Touch Probe Cable
Micro-USB Cable
48V PSU
5V PSU
Twin Ferrule Connectors
Multimeter
Connector Crimp Tool
Level Converter
Definite Purpose Contactor DIN Rail
DIN Rail Terminal Blocks
Optocoupler
Optocoupler Mount
Fan Grill Covers
In-Line Fuses
Tape measure
9 Wire Ducts
Contactor Drill Guide
Ruler / Scale
Ferrule Connector Assortment Ideal Wire Stripper Tool
22 AWG Wire Assortment
Solder
2-Port Small Terminal Blocks Heat Set Insert Assortment M3 Thread Forming Screws
Zip Tie Mounts
Zip Ties
M4x40 Bolts and Nuts
M5x10 Bolts and Nuts

1. Start by taking the 10 foot long wire duct channel and make a mark at around 14.25” from one end. Use scissors to cut this section out in between the grooves as shown below. Note: Wire duct distances are approximate; if a measurement does not fall within a slotted groove, make the cut inside the nearest groove. Repeat to cut out another 14.25” segment.
2. Next, mark off a section approximately 11.75” long and cut out with scissors. Repeat to cut out another 11.75” segment.
3. Next, mark off a section approximately 10.25” long and cut out with scissors.

/

4. Next, mark off a section approximately 5.5” long and cut out with scissors.
5. Next, mark off a section approximately 4.75" long and cut out with scissors.
6. Finally, cut the remaining wire duct segment in half to produce two sections approximately 3.25” long. Cut ~1” off of one of the segments so you have one 3.25” segment and one 2.25” segment.

7. Slide the wire duct lid onto one of the 14.25” segments from Step 1 and make sure that the ends line up. Cut out the same size lid as the segment used as shown in the picture below.
8. Repeat Step 7 for all 9 wire duct segments until you have 9 ducts and 9 lids as shown below.

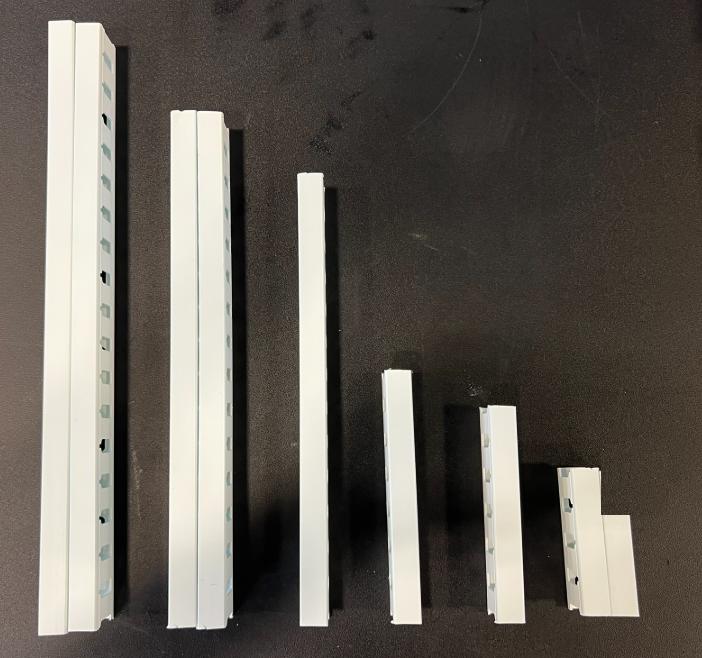
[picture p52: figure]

9. Using two M3x10 screws, mount one of the 14.25” segments of wire ducts on the last row of grids on the long side of the grid plate. Repeat with the other 14.25” segment on the other long side of the grid plate. The result is shown below.
10. Mount the 10.25” wire duct segment onto one of the shorter sides with two M3x10 bolts as shown below.

11. Mount one of the 11.75” wire duct segments 7.5” to the left of the 10.25” segment from Step 10 using two M3x10 bolts. Note that 7.5” distance between the ducts is measured from the left edge of each segment, as shown below.
12. Mount the other 11.75” segment 5.5” to the left of the other 11.75" segment from Step 11 using two M3x10 bolts. Note that the 5.5” distance between the ducts is measured from the left edge of each segment, as shown below.

13. Mount the 4.75” segment 6” up from the bottom of the lower 14.25” segment from Step 9. Note that the 6” distance between the ducts is measured from the bottom edge of each segment, as shown below.
14. Mount the 5.5” wire duct segment on the far left side of the grid plate using two M3x10 bolts. Make sure the bottom part of the wire duct matches up with the bottom grid on the far left column of grids, as shown below.

15. Mount the 2.25” wire duct segment 1 grid above and to the right of the 5.5” segment from Step 14 using one M3x10 bolt. Make sure that the end of the channel lines up with one of the grooves from the 11.75” segment to the right, as shown below.
16. Mount the 3.25” wire duct segment 3.5” from the 10.25” wire duct segment on the far right side using two M3x10 bolts. Note that the 3.5” distance between the two segments is measured from the left side of each channel, as shown below.

17. This concludes the grid plate preparation. The final result should look like the image below.
18. Using two #6 screws, mount the VFD into the top right corner of the grid plate. Leave about gap of about 1 grid between the VFD and wire ducts on its right and top sides. Note that the VFD may not be perfectly square due to grid spacing not lining up exactly with mounting holes.
19. Using two M4 bolts, attach the PSU mounting plate to the PSU as shown below.

20. Using two #6 screws, mount the PSU to the grid plate to the left of the VFD as shown below.
21. Using two M3x10 bolts, mount one of the DM556 drivers to the left of the PSU. The finned side should be facing the back of the grid plate and should be pushed all the way up against the wire channel.

22. Repeat Step 21 to add the other two DM556 drivers in front of the first one. Make sure to leave about 3 grid spaces worth of distance in between each driver as shown in the picture below.
23. Select the driver settings for the DM566 drivers.

1: ON
2: OFF
3: ON
4: OFF
5: ON
6: ON
7: OFF
8: ON

24. Using two M3x10 bolts, mount the Teensy 4.1 breakout board into the bottom left section of the grid plate as shown below. The top screw should be all the way up against the upper wire channel, and the bottom screw should have 5 grid spaces between it and the bottom wire channel.
25. Using two M3x10 bolts, mount the 5V PSU to the top left section of the grid plate. There should be 2-3 grid spaces between the top of the 5V PSU and the top wire channel, as shown below.
26. Using two M3x10 bolts and two washers, mount the DIN rail in front of the PSU as shown below.

27. Using four M3x10 bolts, mount the two bus bars in front of the VFD as shown below.
28. Using two M3x10 bolts, mount the 12V step down converter in the section in front of the three DM556 drivers as shown in the picture below. Leave the wires floating and unconnected for now.

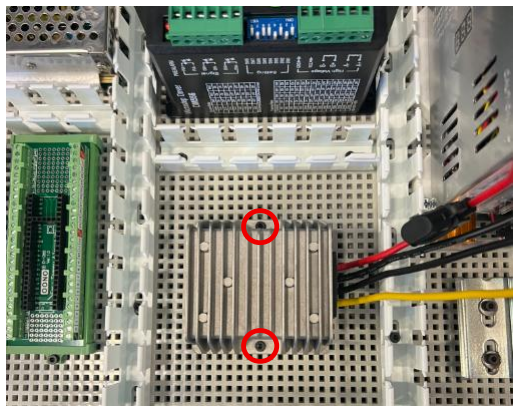
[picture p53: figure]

29. Find and set aside the white optocoupler mount and four M3x6x5 heat set inserts as shown below.

30. Using a soldering iron set to approximately 450 °F, use a light to moderate amount of force to push one of the heat set inserts into one of the four holes on top of the optocoupler mount as shown below. The heat set insert should finish flush with top of the mount.
31. Repeat Step 30 for the other heat set insert in the hole diagonal from the previous step. Then, install two heat set inserts in the two holes circled below using the same technique.
32. The two previous steps should result in the product shown below.

33. Using four M3x10 screws (two for each optocoupler) mount the 4-channel optocoupler and single channel optocoupler onto the board as shown. Note: for the single channel optocoupler, do NOT tighten down all the way, leave some space as shown.
34. Using two M3x10 screws, insert the optocoupler mount directly over the 12V stepdown converter as shown in the image below. Note that the mount may be slightly crooked due to grid spacing. Make sure the side with the blue ports is on the side facing the DM556 drivers.

35. Grab three orange, three yellow, two black, and two white DIN rail terminal blocks. Snap the connectors together in the orientation shown using the clips on the sides of the terminal blocks.
36. Snap the terminal blocks onto the DIN rail in the orientation shown below. Note, it is easier to put the terminal blocks on the DIN rail and snap two on at a time rather than pressing all ten together.
37. Cut two black 22AWG wires to 55 mm and strip both sides to 8 mm. To strip the wires, use the Weicon tool and set the backstop to 8 mm, then squeeze to pull back the insulation as shown.

38. Crimp a 22AWG ferrule connector to one side of one of the 55 mm black wires.
39. Crimp a 22AWG twin ferrule connector onto both 55 mm black wires.

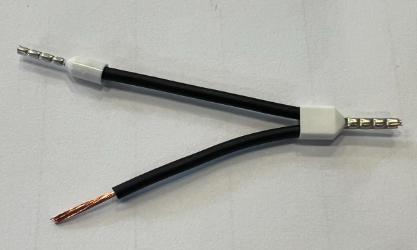
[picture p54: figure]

40. Cut a black 22AWG wire to 110 mm and strip both ends to 8 mm.
41. Crimp a 22AWG twin ferrule connector between the open 55 mm lead and the 110 mm wire.
42. Cut out another 55 mm wire and another 110 mm wire and strip both ends to 8 mm.
43. Attach the two 110 mm wires and the new 55 mm wire together with a 20AWG twin ferrule connector as shown below.

44. Cut out another 55 mm wire and strip both ends to 8 mm.
45. Crimp a 22AWG twin ferrule connector between the open 55 mm lead from Step 43 and the new 55 mm wire. Then crimp a 22AWG ferrule connector onto the open end of the new 55 mm wire.
46. Cut another 55 mm black wire and a new 150 mm black wire and strip both ends to 8 mm.
47. Attach the open 110 mm lead from Step 43, the new 55 mm wire, and the new 150 mm wire together by crimping a 20AWG twin ferrule connector on them as shown below.

48. Cut out another 55 mm wire and strip both ends to 8 mm.
49. Repeat Step 45 with the open 55 mm lead from Step 47 and the new 55 mm wire form Step 48. Crimp a 22AWG ferrule connector onto the free end of the 150 mm lead.
50. Remove the terminal blocks from the signal side of the DM556 motor drivers. Attach the jumped ground connections from Step 49 to the ENA-, DIR-, and PUL- pins on the motor drivers outlined in red.

51. Begin preparing the rest of the signal wires. Cut a 4-core shielded cable to 11 in. and strip back 50 mm (2 in.) of insulation on one side. Note, the easiest way to strip the 4-core shielded cable is to use the Ideal Swivel-Blade Cable Stripper to cut the required distance lengthwise. Then, using wire cutters, circumferentially cut at the base of the first cut to peel the insulation off, as shown on the next page.

52. Twist the stranded shielding wire together and remove the shielded foil and red wire as shown.
53. Strip the ends of the blue, green, and yellow wires to 8 mm. Crimp 22AWG ferrule connectors onto these wires, leaving the stranded shielded wire free.
54. Strip the other end to 50 mm as well, and repeat Step 52, except you can also cut off / remove the stranded shielded wire as well. Repeat Step 53 as well to produce the final result below.

55. Cut a 4-core shielded cable to 23 in. and strip one end to 50 mm, removing the red wire and foil. Strip the blue, green, and yellow wires to 8 mm and attach 22AWG ferrule connector to them.
56. Strip 12.5 inches of insulation off of the other side and remove the red wire and foil. Then cut off all but 55 mm of the blue and green wire, leaving the yellow wire at full length. Strip these new lengths to 8 mm and attach 22AWG ferrule connectors as shown.
57. Strip the end of the yellow wire to 8 mm and crimp a 22AWG ferrule connector to the end to produce the final result shown below.

58. Cut a 4-core shielded cable to 25 in. and strip one end to 50 mm, removing the red wire and foil. Strip the blue, green, and yellow wires to 8 mm and attach 22AWG ferrule connector to them.

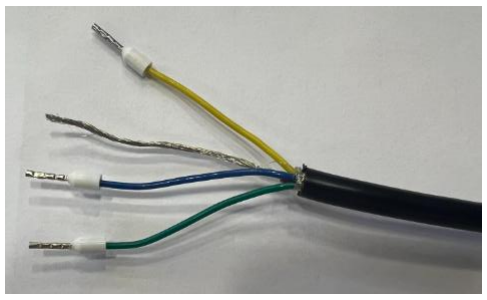
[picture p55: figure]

59. Strip 12.5 inches of insulation off of the other side and remove the red wire and foil. Then cut off all but 55 mm of the blue and green wire, leaving the yellow wire at full length. Strip these new lengths to 8 mm and attach 22AWG ferrule connectors as shown.
60. Strip the end of the yellow wire to 8 mm and crimp a 22AWG ferrule connector to the end to produce the final result shown below.

61. First, take the 11-in. 4-core shielded cable from Step 54. Using the side with the stranded shielding, plug in the blue, green, and yellow wires into the following ports. Note, leave the long black wire coming from the PUL- port on the front drive unconnected on its free end for now.
a. Blue wire = PUL+
b. Green wire = DIR+
c. Yellow wire = ENA+
62. Repeat for the 23 in. and 25 in. wires to produce the result shown below.
63. Starting with the 11 in. shielded cable, route the cord in front of the DM556 driver and through the wire channels as shown below.

64. Connect the blue, green, and yellow wires from the 11 in. cable into the Teensy 4.1 following the GRBLHAL reference page. The front DM556 driver is now the X-axis drive.
a. Blue: PUL+ → Pin 2: Step X
b. Green: DIR+ → Pin 3: Direction X
c. Yellow: ENA+ → Pin 10: Enable X
65. Now with the 23 in. shielded cable from the middle DM556 driver, route the cord in front the middle driver and through the wire channels as shown below.

66. Connect the blue, green, and yellow wires from the 23 in. cable into the Teensy 4.1 following the GRBLHAL reference page. The middle DM556 driver is now the Y-axis drive.
a. Blue: PUL+ → Pin 4: Step Y
b. Green: DIR+ → Pin 5: Direction Y
c. Yellow: ENA+ → Pin 40: Enable Y
67. Finally with the 25 in. shielded cable from the back DM556 driver, route the cord in front of the back driver and through the wire channels as shown below.

68. Connect the blue, green, and yellow wires from the 25 in. cable into the Teensy 4.1 following the GRBLHAL reference page. The back DM556 driver is now the Z-axis drive.
a. Blue: PUL+ → Pin 6: Step Z
b. Green: DIR+ → Pin 7: Direction Z
c. Yellow: ENA+ → Pin 39: Enable Z
69. Starting with the 11 in. wire, fold the end of the stranded shielding wire over on itself as shown.

70. Using the connector crimp tool, crimp the folded over stranded shielding wire into one end of a red butt connector as shown below.
71. Repeat Step 69-70 for the 23 in. and 25 in. wires to produce the result shown below.

72. Cut a 24 in., a 26 in., and a 28 in. length of 16AWG green wire as shown below.
73. Starting with the 24 in. wire, strip one end to 8 mm and crimp into the red butt connector on the X-axis drive (front DM556 driver). Route in the same channel as the shielded cable.
74. Strip one end of the 26 in. green wire to 8 mm and crimp into the red butt connector on the Y-axis drive (middle DM556 driver). Route in the same channel as the shielded cable.

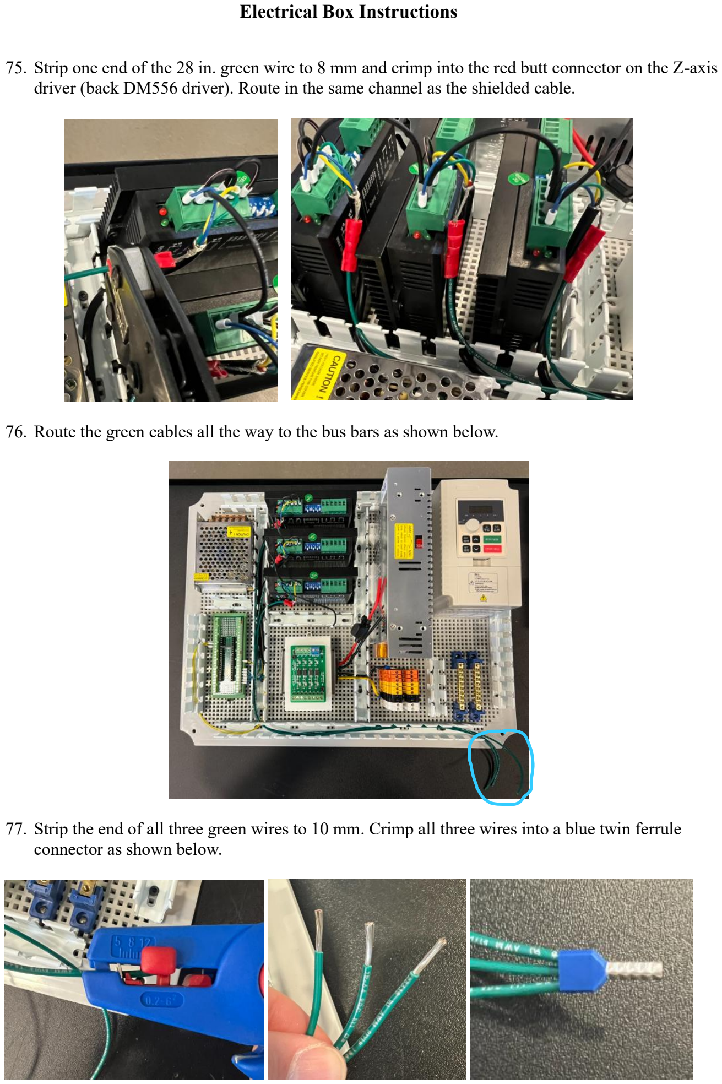
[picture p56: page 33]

75. Strip one end of the 28 in. green wire to 8 mm and crimp into the red butt connector on the Z-axis driver (back DM556 driver). Route in the same channel as the shielded cable.
76. Route the green cables all the way to the bus bars as shown below.
77. Strip the end of all three green wires to 10 mm. Crimp all three wires into a blue twin ferrule connector as shown below.

78. Insert these wires into the bus bar and tighten into place.
79. Cut a 16AWG green wire to 9 in., strip both ends to 8 mm, and crimp a 16AWG ferrule connector on each end.
80. Insert one end of the green wire into one of the bus bars and tighten down. Route the wire through the wire channels and insert the other end into the other bus bar, as shown below.

81. Cut a 16AWG red wire to 11 in. and strip both ends to 8 mm. Crimp a 16AWG ferrule connector onto one end and crimp an (M4)#8 or (M5)#10 fork terminal onto the other end as shown. When crimping these connectors, make sure the split in the connector contacts the top jaw of the tool as shown.
82. Insert the ferrule connector side into the VCC port on the High Voltage side of the X-axis DM556 drive and tighten to secure. Insert the fork connector side into the bottom +V port on the 48V PSU and tighten to secure. Note, it may be necessary to scoot the colored DIN rail terminal blocks down to assist in inserting the fork connectors.

83. Cut a 16AWG red wire to 13 in. and crimp both ends to 8 mm. Crimp a 16AWG ferrule connector onto one end and crimp an (M4)#8 or (M5)#10 fork terminal onto the other end as shown.
84. Insert the ferrule connector side into the VCC port on the High Voltage side of the Y-axis DM556 drive and tighten to secure. Insert the fork connector side into the middle +V port on the 48V PSU and tighten to secure.
85. Cut a 16AWG red wire to 15 in. and strip both ends to 8 mm. Crimp a 16AWG ferrule connector onto one end and crimp an (M4)#8 or (M5)#10 fork terminal onto the other end as shown.

86. Insert the ferrule connector side into the VCC port on the High Voltage side of the Z-axis DM556 drive and tighten to secure. Insert the fork connector side into the top +V port on the 48V PSU and tighten to secure.
87. Cut a 23 in., a 25 in., and a 27 in. length of 16AWG green wire as shown below. Strip one end of all three wires to 8 mm, and the other end of all three wires to 10 mm.
88. Crimp a 16AWG ferrule connector onto the three sides stripped to 8 mm.

89. Starting with the 23 in. wire, insert the ferrule connector into the GND port on the High Voltage side of the X-axis DM556 drive and tighten to secure. Route the remaining wire and 10 mm stripped end to the bus bar as shown below.
90. Now with the 25 in. wire, insert the ferrule connector into the GND port on the High Voltage side of the Y-axis DM556 drive and tighten to secure. Route the remaining wire and 10 mm stripped end to the bus bar as shown below.

91. Finally with the 27 in. wire, insert the ferrule connector into the GND port on the High Voltage side of the Z-axis DM556 drive and tighten to secure. Route the remaining wire and 10 mm stripped end to the bus bar as shown below.

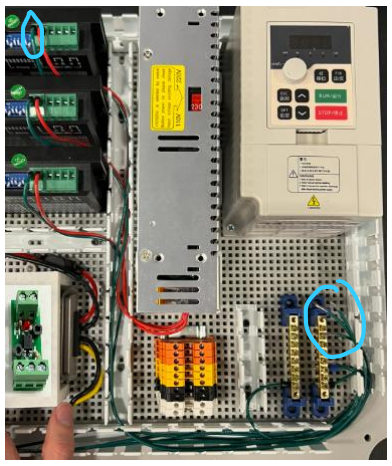
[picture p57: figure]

92. Crimp a 14AWG twin ferrule connector onto all three of the 10 mm stripped ends of the green wires as shown.
93. Insert the twin ferrule connector with all three wires into the bus bar as shown and tighten to secure.

94. Cut a 6 in. and a 7 in. length of 16AWG green wire and strip both ends of both wires to 8 mm. On one side of each wire, crimp a 16AWG ferrule connector. On the other side of each wire, crimp a (M4)#8 or (M5)#10 fork connector as shown below.
95. Secure the fork connector on the 6 in. wire into the middle -V port on the 48V PSU and route the remaining wire and ferrule connector to the bus bar as shown.
96. Secure the fork connector on the 7 in. wire into the ground port on the 48V PSU and route the remaining wire and ferrule connector to the bus bar as shown.

97. Next, grab the logic level converter and the four small terminal blocks. Insert one of the terminal blocks into the HV1 and HV2 pins on the level converter as shown. Make sure it is flush.
98. Hold the level converter in place with a set of alligator clips. Once secured, solder the two pins in place as shown.
99. Insert a new terminal block into the HV and GND pins next to the HV1 and HV2 pins.

100. Hold the two terminal blocks together with alligator clips and solder the new terminal block in place.
101. Repeat Steps 97-100 on the other side of the level converter with the LV1, LV2, LV, and GND pins to produce the result shown below.
102. Set aside the three components shown below: level converter, zip tie, adhesive zip tie mount.

103. Insert the zip tie through the zip tie mount and then mount the level converter on top of the mount as shown below. Tighten the zip tie down to secure the level converter.
104. Peel the sticker off of the back of the adhesive mount and install the mount below the Teensy 4.1 on the grid plate as shown below. Make sure the level converter is oriented correctly with the terminal blocks on the bottom.

105. Cut out a 28 in. length of 4-core shielded cable. Strip one end to 35 mm and remove the red wire and foil from this side. Strip the blue, green, and yellow wires to 8 mm and crimp 22 AWG ferrule connectors onto their ends.
106. Strip the other end to 150 mm and remove the red wire, foil, and stranded shielding. Trim the green wire to 90 mm, trim the blue wire to 60 mm, and leave the yellow wire at its full 150 mm length. Strip the ends of these three wires to 8 mm and crimp 22AWG ferrule connectors on their ends.

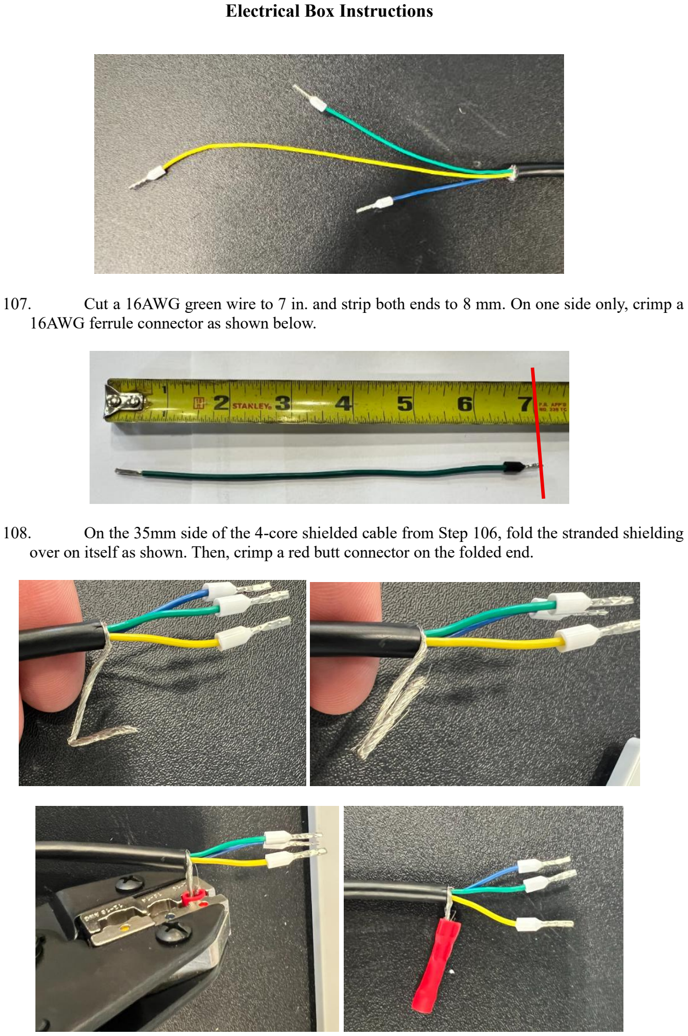
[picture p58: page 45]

107. Cut a 16AWG green wire to 7 in. and strip both ends to 8 mm. On one side only, crimp a 16AWG ferrule connector as shown below.
108. On the 35mm side of the 4-core shielded cable from Step 106, fold the stranded shielding over on itself as shown. Then, crimp a red butt connector on the folded end.

109. Crimp the open end of the 7 in. green wire from Step 107 into the other end of the red butt connector as shown.
110. Insert the 35 mm end of the 4-core shielded cable through into the VFD as shown and make the following connections:
a. Blue → AI1
b. Green → GND
c. Yellow → X1
111. Route the shielded cable and green wire through the wire channels as shown. Ground the green wire into the bus bar.

112. Cut a 16AWG green wire to 8.5 in. and strip both ends to 8 mm. Crimp a 16AWG ferrule connector on one end and a (M4)#8 fork connector on the other end.
113. Insert the fork connector into the ground terminal on the VFD and route the cable to the bus bar.
114. Route the 4-core shielded cable through the wire ducts along the bottom of the box to the Teensy 4.1 as shown. Connect the yellow wire to pin 12 and the green wire to a GND port, as highlighted in the photo below. Leave the blue wire unconnected for now.

115. Cut two 22AWG solid core wires: a 70 mm length and a 100 mm length. Strip both ends to 5 mm. Bend the 70 mm wire to form the shape shown below.
116. Insert the bent 70 mm wire into one of the GND ports on the level converter and jump the bent wire to the GND port on the other side of the level converter as well. On the left side, also insert the 100 mm green wire and tighten to secure. Route the 100 mm cable to the GND port shown on the Teensy 4.1 below.
117. Cut a blue 22AWG solid core wire to 140 mm and strip both ends to 5 mm.

118. Connect one end of the blue wire into the LV1 port on the level converter (circled in picture below) and route the other side through the cable trays and into pin 13 on the Teensy 4.1.
119. Cut a red 22AWG solid core wire to 100 mm and strip both ends to 5 mm.
120. Connect one end of the red wire to the LV port on the level converter (circled in the picture below) and route the other side through the cable trays and into the 3V3 port on the Teensy 4.1.

121. Insert the hanging blue wire from the 4-core shielded cable in Step 114 into the HV1 port on the level converter (circled in the picture below).
122. Cut a 16AWG red wire to 7 in. and strip both ends to 8 mm. Crimp a (M4)#8 or (M5)#10 fork connector onto one end and leave the other end stranded.
123. Find the red wire coming out of the 12V step down transformer (it should have an in-line fuse on it). Cut off the tinned end of the wire as shown below. Be careful not to remove too much wire, a few millimeters should do. Then strip the end to 8 mm.

124. Crimp a red butt connector onto the end of this wire as shown.
125. Take the red wire from Step 122 and insert the free stranded end into the other end of the butt connector. Crimp tightly to make a secure connection.

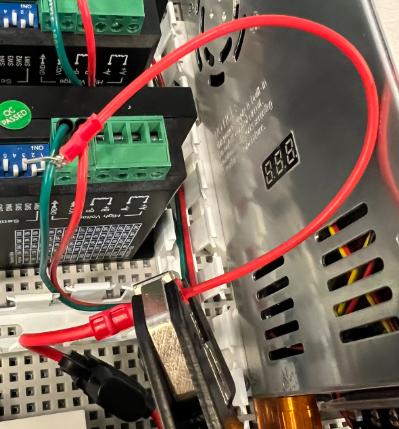
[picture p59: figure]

126. Route the cable through the cable trays as shown below and insert the fork connector into the top +V port on the 48V PSU. Note that it will be doubled up with the Z-axis drive.

127. Locate the black wire directly next to the red wire from the 12V step down transformer. Cut off the tinned end of the wire, being careful not to remove too much wire. Strip the end to 8 mm.
128. Crimp an (M4)#8 or (M5)#10 fork connector onto the free end as shown. Insert the black wire into the -V port shown below and secure. Note, this cable may not be long enough to fit through the cable trays, so it can route straight to this port.
129. Using the wire cutters, cut off the tinned end of the other two wires coming from the 12V stepdown converter, as shown for the yellow wire below. Be careful not to cut off too much wire, a few millimeters is sufficient.

130. Cut the yellow wire to a length of 90 mm from the 12V step down transformer, as shown.
131. Strip the yellow wire to a length of 8mm using the Weicon wire stripping tool as shown below.
132. Crimp a blue 14AWG ferrule connector onto the stripped end of the yellow wire using the Klein crimping tool. Make sure to give a tight squeeze to ensure a proper connection.

133. Repeat Steps 129-132 on the black wire to produce the result shown below.
134. Route both the yellow and black wires through the cable tray to the right of the 12V stepdown converter and insert them into the two terminal slots shown in the image below. To secure the wires, use a flat head screwdriver to tighten from above.

135. Cut a section of black 16AWG wire to 65 mm and strip both ends to 8 mm.
136. Crimp a black 16AWG ferrule connector onto ONE end of the wire.
137. Repeat Steps 135-136 to create an identical 65 mm length of 16AWG wire.
138. Insert the two free stripped ends of both wires into a 16AWG twin ferrule connector. Clamp tightly to ensure a secure connection.

139. Use the result from Step 138 to jump the wires between all three orange terminal blocks on the side closest to the grounding bus bars, as shown below. Note that the twin connector will have to be inserted into the middle orange terminal block vertically in order to fit.
140. Repeat Steps 135-139 with red 16AWG wire to produce the result shown below.
141. Cut two red 22AWG stranded core wires: a 16 in. length and a 17.5 in. length. Strip both ends of each wire to 8 mm. On one side of each wire, crimp 22AWG ferrule connectors, leaving the other two sides uncrimped as shown.


142. Twist the two bare ends of each wire together and crimp an (M4)#8 fork connector onto
both wires as shown below.

143. Insert the fork connector into the +V terminal on the 5V PSU as shown below.

144. Route the 16 in wire along the right side of the Teensy 4.1 to the HV port on the level
converter as shown.

145. Now route the 17.5 in wire along the left side of the Teensy 4.1 to the 5V port on the Teensy 4.1 as shown.
146. Cut a black 22AWG stranded core wire to 17 in. and strip both ends to 8 mm. Crimp a 22AWG ferrule connector on one end and a (M4)#8 fork connector on the other end as shown.
147. Insert the fork connector into the -V port on the 5V PSU. Route the black wire along the left side of the Teensy 4.1 and connect to the bottom left GND port on the Teensy 4.1. Note that there will be two wires in this GND port since the ground from the level converter is already in this port as well.


148. Cut a green 16AWG wire to 27 in. and strip both ends to 8 mm. Crimp a 16AWG ferrule connector on one end and an (M4)#8 fork connector on the other end as shown.
149. Insert the fork connector into the ground terminal on the 5V PSU and route the cable to the bus bar along the back of the box as shown.

150. Cut a red 22AWG stranded core wire to 7 in. and a black 22AWG stranded core wire to 11 in. Strip both ends of each wire to 8 mm and crimp 22AWG ferrule connectors to both sides of each wire.
151. Secure one end of the red wire into the VCC port on the optocoupler. Route the wire through the wire channels to the nearest 3V3 port on the Teensy 4.1 as shown.
152. Secure one end of the black wire to the GND port on the optocoupler. Route the wire through the wire channels to the GND port shown below on the Teensy 4.1.

153. Collect four colors of 22AWG solid core wire: orange, blue, green, and red. Cut the orange wire to 7 in. and the blue, green, and yellow wires to 15 in. Strip both ends of each wire to 5 mm.
154. Arrange the wires in the order orange, blue, green, red. Starting ~1.5 in. from one end, begin twisting the wires together as shown. Stop twisting the wires ~4 in. from the end you started at.
155. Secure the four wires into the optocoupler in the exact order shown in the image below.

156. Install a ferrite over the 6 cables coming out of the output side of the optocoupler as shown.
157. Leaving the orange wire out, twist the blue, green, and red wires together until the last 2 in. of the wire as shown.
158. Route the twisted cables through the cable trays as shown. Insert the orange wire into pin 29 on the Teensy 4.1.

159. Route the remaining blue, green, and red wires as shown below. Insert red into pin 20, green into pin 21, and blue into pin 22 on the Teensy 4.1.
160. Cut three red 16AWG wires to 65 mm and strip both ends to 8 mm. On one side of one of the wires, crimp a 16AWG ferrule connector to produce the three wires shown below.
161. Crimp a 16AWG twin ferrule connector onto the free end of the wire with the ferrule connector and one of the free ends from another wire as shown.

162. Crimp another 16AWG twin ferrule connector between the free end of the wire from Step 160 and the last red wire.
163. Cut a 16AWG red wire to 8.5 in. and strip both ends to 8 mm. Crimp a 16AWG ferrule connector onto one end, leaving the other end bare.
164. Using one more 16AWG twin ferrule connector, crimp the free end of the 8.5 in. wire to the free end of the result from Step 161 as shown below.
165. Insert the wire assembly into the 1+, 2+, 3+, and 4+ ports on the optocoupler as shown below. Make sure that the long wire’s twin ferrule connector is in the 1+ port.

166. Route the long red wire to the yellow DIN rail terminal block shown below.


167. Cut a 16AWG white wire to 21 in. and strip both ends to 8 mm. Crimp a 16AWG ferrule connector on one end and an (M4)#8 fork connector on the other end.
168. Insert the ferrule connector into an open white DIN rail terminal block and route to the Neutral (‘N’) terminal on the 5V PSU as shown.

169. Cut a 16AWG black wire to 21 in. and strip both ends to 8 mm. Crimp a 16AWG ferrule connector to one end and an (M4)#8 fork connector to the other end.
170. Insert the ferrule connector into an open black DIN rail terminal block. Route the wire through the wire ducts to the Live (‘L’) terminal on the 5V PSU as shown.
171. For the next set of steps, set the grid plate inside the provided electrical box and mount with the included screws.

172. Locate the two Thermalright TL-C12 120MM Fans. Set aside one fan and remove it from its packaging.
173. Cut off the 4-pin port on the end of the wire as shown below. This port can be thrown away.
174. After cutting off the 4-pin port, remove the sheathing around the four wires as shown below. This sheathing can be thrown away as well.

175. Split the four wires directly down the middle, keeping the left two connected and the right two connected as shown. Separate these wires all the way down to the frame of the fan.
176. Locate the two wires shown in the picture on the left below. The wire with gray rectangles is the ground, and the wire connected to it with writing on it is the power. Being careful not to cut these wires, use scissors or wire cutters to remove the other two wires from Step 174 as shown.
177. Repeat Steps 171-175 for the other fan to produce the results below.

178. Locate the two 3D printed fan grills shown below.
179. Set one of the grills on top of one of the fans exactly as shown, with the blade side facing up. Insert four M4x40 bolts through the four mounting holes as shown.
180. On the left side of the electrical box, there should be a cutout right next to the 5V PSU. Using the fan from Step 178, feed the wire through the bottom left most hole in the box as shown. Make sure that the fan is rotated such that the wire is coming out of the bottom left side of the fan.

181. Insert the four M4x40 bolts through the four holes on the box and tighten a nut on the other side using a screw driver and pliers as shown.
182. Set the other fan grill on top of the other fan exactly as shown, this time with the frame side facing up. Insert four M4x40 bolts through the mounting holes to produce the following.

183. On the right side of the electrical box, there should be a cutout right next to the VFD. Using the fan from Step 181, feed the wire through the bottom right most hole in the box as shown. Make sure that the fan is rotated such that the wire is coming out of the bottom right side of the fan.
184. Repeat Step 180 with the new fan to produce the result below.
185. The two wires from each fan should meet up in the back middle of the box as shown.

186. For both set of two wires, peel 50 mm of the wires apart as shown.
187. Strip 12 mm off of all four wires.


188. Twist the two ground wires (the ones with the grey rectangles on the insulation) together. Then, fold the twisted wire in half as shown.

189. Crimp a red butt connector over the two wires. Then, color the connector black to indicate ground.
190. Repeat Steps for 187-188 for the other two wires, but do not color the connector black since this is the power line. The result is shown below.
191. Cut out two 9 in. lengths of 22AWG stranded core wire. Strip one end of each wire to 8 mm and strip the other end to 12 mm.

192. Starting with the red wire, fold the stripped stranded end in half and crimp into the other end of the power (red) butt connector as shown.
193. Now fold the stripped stranded end of the black wire in half and crimp into the other end of the ground (colored black) butt connector as shown.

194. Route these wires through the middle wire channel in the box. Leave the 8 mm stripped ends disconnected for now.
195. Cut a red and black 22AWG stranded core wire, both to 7 in. Strip both ends of each to 8 mm.
196. Insert one end of the red wire from Step 195 and the free stripped end of the red wire from Steps 193-194 into a grey twin ferrule connector and crimp to secure.

197. Insert one end of the black wire from Step 195 and the free stripped end of the black wire from Steps 193-194 into a grey twin ferrule connector and crimp to secure.
198. Insert the twin connector from the red wires into the last remaining yellow DIN rail terminal block and the twin connector from the black wires into an orange DIN rail terminal block as shown.


199. On the free ends of the red and black wires from the previous steps, crimp a 22AWG white
ferrule connector as shown.

200. Route the wires to through the cable trays to the single channel optocoupler. Secure the red
wire into the + INPUT port and the black wire into the – port.

201. Cut three 65 mm lengths of 16AWG green wire and strip both ends of each wire to 8 mm. Crimp a 16AWG ferrule connector onto one end of one wire.
202. Crimp a 16AWG twin ferrule connector onto the free end of the wire with the ferrule connector and one of the free ends from another wire as shown.
203. Crimp the other 65 mm wire onto the free end of Step 195 with another 16AWG twin ferrule connector as shown.
204. Cut a 16AWG green wire to 12 in. and strip both ends to 8 mm. Crimp a 16AWG ferrule connector onto one end of the wire.

205. Crimp the 12 in. wire and the free end of the 65 mm wire from Step 196 together with a 16AWG twin ferrule connector to produce the result shown below.
206. Grab four 3-port terminal blocks.
207. Connect the green wire assembly from Step 198 into the four 3-port terminal blocks as shown below.
208. Cut three 65 mm lengths of 16AWG black wire and strip both ends of each wire to 8 mm. Crimp a 16AWG ferrule connector onto one end of one wire.

209. Cut out a 9 in. 16AWG black wire and strip both ends to 8 mm. Crimp a 16AWG ferrule connector onto one end of the wire.
210. Repeat Steps 195-198 but with the black wires from the previous steps to produce the following.
211. Insert the assemble black wire into the four 3-port terminal blocks as shown.
212. Next cut out four red wires: a 6 in. length, a 6.5 in. length, and two 7 in. lengths.


213. Insert the four red wires into the four 3-port terminal blocks as shown below.

214. Feed the wires through the front left cutout on the electrical box as shown.

215. Route the long black wire into the last remaining orange DIN rail terminal block, and the green wire to the bus bar.
216. Feed the four red wires through the wire channels and into the optocoupler as shown. The order of the red wires should match exactly with the order of the four ports (1-, 2-, 3-, 4-) on optocoupler.
217. Cut a 22AWG solid core red wire to 10 in., a 22AWG solid core green wire to 12 in., and a 22AWG solid core orange wire to 12 in. as shown below.


218. Line up one end of each three wires. Begin twisting the wires together about 1 in. from the end as shown.
219. Twist all three wires together until there is about 2.5 in. of red wire remaining. At this point, twist just the orange and green wires together, leaving the red wire by itself. Twist the green and orange wires until there is about 2 – 2.5 in. of each, at which point you can leave them untwisted as shown.
220. Insert the side of the twisted wire from Step 218 into a 3-port terminal block as shown. Make sure the order is exactly as shown in the photo.

221. Place this new 3-port terminal block to the right of the terminal blocks from Step 214 as shown.
222. Route the twisted cable through the cable trays to the left side of the Teensy 4.1. Insert the red wire into the 5V port on the bottom left side of the Teensy 4.1. Note: there is already a connector in this 5V port, so you will have to stack up two wires in this terminal.
223. Insert the green wire into the GND port and the orange wire into pin 15 on the Teensy 4.1 as shown.

224. Collect three colors of 22AWG solid core wire: blue, green, and red. Cut the red wire to 12 in., and the blue and green wires to 16.5 in. Strip both ends of each wire to 5 mm.
225. Acquire the blue, green, and red wires and begin twisting together starting ~1 in. from the ends as shown below.
226. Twist ~8.5 to 9 in. of the three wires together as shown below.

227. Leaving the red wire free now, twist the blue and green wires together until the last ~2 in. of the wires as shown.
228. Insert the three wires into the single channel optocoupler as shown below. Red should be in the VCC port, blue in the OUT port, and green in the GND port. Route twisted cable to Teensy.
229. Insert the red wire into the 3.3V port on the Teensy as shown below.

230. Insert the blue wire into pin 14, and the green wire into GND. Note, there is already a green wire in the GND port being used. This is fine, just fit both green wires into the port.
231. Acquire the front panel shown below.
232. From the inside of the box, insert the five 3-port terminal blocks into the front panel as demonstrated below.

233. Acquire the slide connector piece shown below.
234. Slide the slide connector over the five 3-port terminal blocks to lock them in place, as shown below.

235. Leave the front panel disconnected from the box for the moment. From the outside of the box, it should look like the image below.
236. Cut out three 21 in. lengths of 4-core shielded cable. Strip one end of each wire to 50 mm and the other end of each wire to 80 mm.

237. On the 50 mm stripped side, remove the foil and stranded wire. Strip the red, blue, green, and yellow wires to 8 mm and crimp a 22 AWG ferrule connector on each wire. Repeat for all three wires.
238. On the 80 mm side, remove just the foil, leaving the stranded wire connected as shown.


239. Cut out three ~25 mm lengths of black heat shrink.

240. Apply the heat shrink around the base of the 80 mm stripped side of each cable as shown.
241. Strip the red, blue, green, and yellow wires on the 80 mm side of each cable to 8 mm and crimp 22AWG ferrule connectors to each.
242. Cut out two 100 mm lengths of black 22AWG stranded core wire and strip both ends of each to 8 mm.

243. Cut out a 12 in. length of 16AWG green wire and strip both ends to 8 mm. Crimp a 16AWG ferrule connector on one end, leaving the other end stranded.
244. Twist one of the 100 mm black wires onto the shielded section of one of the 4-core shielded cables as shown below. Crimp a black twin ferrule connector onto these two wires.
245. Twist the other end of the 100 mm black wire from Step 244 onto the other black 100 mm wire and the stranded wire from another one of the 4-core shielded cables as shown. Crimp a black twin ferrule connector onto these three wires.

246. Twist the other end of the 100 mm black wire from Step 245 onto the stranded wire from the final 4-core shielded cable and the stranded wire from the free side of the green wire as shown. Crimp a black twin ferrule connector onto these three wires.
247. Apply electrical tape around the exposed stranded shielding from the 4-core shielded cables as shown.

248. Insert and secure the wire assemblies from Step 247 into three 5-port terminal blocks as shown below. Note, make sure that the wire orders are exactly as shown below.
249. Insert the three 5-port terminal blocks into the ‘X MOTOR’, ‘Y MOTOR’, and ‘Z MOTOR’ slots on the front panel from inside the box as shown. Make sure that the terminal block with the green wire coming out of it is in the ‘Z MOTOR’ slot.
250. Slide the other slide connector over the three terminal blocks to lock them in place.

251. The front panel can now be mounted onto the box using four M4x16 bolts and four M4 nuts. Use a screw driver and pliers to secure the nuts on the bolts.
252. All three 4-core shielded cables will now be routed through the middle wire duct in the box as shown. Note that two of the cables can go straight from the bottom channel to the middle channel, where as one may have to make a “shortcut” due to space constraints. The final result after Steps 253-256 will look like the image shown below.

253. Route the 4-core shielded cable from the ‘Z MOTOR’ to the Z-axis drive through the middle wire duct in the box as shown. Secure the four ferrule connectors on the blue, yellow, green, and red wires on the Z-axis’s High Voltage terminal block exactly as shown.
a. Blue → B-
b. Yellow → B+
c. Green → A-
d. Red → A+
254. Route the green cable from the ‘Z MOTOR’ port to the bus bar as shown.

255. Route the 4-core shielded cable from the ‘Y MOTOR’ to the Y-axis drive through the middle wire duct in the box as shown. Secure the four ferrule connectors on the blue, yellow, green, and red wires on the Y-axis’s High Voltage terminal block exactly as shown.
256. Route the 4-core shielded cable from the ‘X MOTOR’ to the X-axis drive through the middle wire duct in the box as shown. Secure the four ferrule connectors on the blue, yellow, green, and red wires on the X-axis’s High Voltage terminal block exactly as shown.
257. Acquire four zip ties and four zip tie mounts as shown below.

258. Take the adhesive off of the zip tie mounts and install in the locations shown below. The top of the top two zip tie mounts should be in line with the top of the square cutout as shown. The top of the bottom two zip ties should be ~25 mm above the bottom of the square cutout.
259. Starting with the top left mount, slide a zip tie horizontally through the mount as shown. Repeat for the bottom mount as well.


260. Place an in-line fuse over the mount as shown. Make sure that the fuse is positioned such that the fuse box opens upwards. Tighten both zip ties and cut off the extra to produce the following.
261. Repeat Steps 259-260 on the other side to produce the following.


262. Strip the top red wires on both fuse lines to 8 mm and crimp a red quick-disconnect
connector onto both.

263. Using four M4x16 bolts and M4 nuts, secure the other front panel in place as shown.

264. Acquire two IEC receptables and secure into the ‘PSU’ and ‘VFD’ ports with four #6
screws.

265. Plug in the red quick connects from Step 262 to the IEC receptacles as shown below.
266. Cut two 9 in. 16AWG green wires and strip both ends to 8 mm. Crimp a 16AWG ferrule connector on one side of both wires, and a red quick connect on the other sides.
267. Plug the 9 in. green wires into the ground terminal on the IEC receptacles as shown. Route both wires to the bus bar and secure.

268. Acquire the Definite Purpose Contactor and 3D printed drill guide shown below.
269. Slide the 3D printed drill guide onto the outside of the box as shown. When looking down at the top of the box with the stainless steel latches facing you, the guide will fit on the bottom right side of the box. Make sure the stoppers are flush against the side and bottom of the box. Tape in place to secure.
270. Using a sharpie, mark the location of the holes as shown. Once all four are marked, you can remove the guide from its position.

271. Using a drill and a 5.5 mm bit, drill each of the four holes out. Note, the drill bit tends to walk / slide out of position without careful attention. Try to make sure the bit stays directly over the sharpie mark or punch the holes first with a center punch if one is available to prevent this.
272. Using four M5x10 bolts and four M5 nuts, secure the contactor on the inside of the box as shown. Make sure that the side with the L1, L2, and L3 terminals is facing the VFD, and the side with the T1, T2, and T3 terminals is facing the IEC receptacles.
273. Cut a white 16AWG wire to 12 in. and strip both ends to 8 mm. Crimp a red quick-connect on one end and an (M4)#8 fork connector on the other.

274. Insert the quick-connect onto the Neutral port on the PSU’s IEC as shown.
275. Route the cable through the middle cable tray and to the 48V PSU as shown. Secure the fork connector into the Neutral (N) terminal on the 48V PSU.
276. Cut out a white 16AWG wire to 65 mm and strip both ends to 8 mm. Crimp a 16AWG ferrule connector onto one end.

277. Cut out a white 16 AWG wire to 8 in. and strip both ends to 8 mm. Crimp a red quick-connect connector onto one end of the wire.
278. Using a 16AWG twin ferrule connector, crimp the free ends of the two white wires together.
279. Insert the quick-connect onto the Neutral port on the VFD’s IEC receptacle as shown.


280. Route the white cable through the cable trays and to the DIN rail terminal blocks. Insert the twin ferrule connector into one of the white terminal blocks and jump the 65 mm cable to the other white terminal block as shown.
281. Cut two white 16AWG wires, one to 17.5 in. and one to 9.5 in. Strip both ends of each wire to 8 mm. On the 17.5 in. wire, crimp a red quick-connect on one side and a 16AWG ferrule connector on the other. On the 10 in. wire, crimp a red quick-connect on one side and an (M4)#8 fork connector on the other.


282. Insert the 16AWG ferrule connector of the 17.5 in. white wire into the open white DIN
rail terminal block as shown. Route the white wire through the bottom channel and under the
Contactor.

283. Plug the quick-connect from the 17.5 in. wire into one of the A2 ports on the Definite
Purpose Contactor as shown.

284. Plug the quick-connect on the 9.5 in. wire into the other A2 port as shown and route the side with the (M4)#8 fork connector through the cable tray to the VFD. Secure the fork connector into the Neutral (N) port on the VFD.
285. Now strip the bottom red wire from the fuse line on the left side (from the inside of the box) of the cut out to 8 mm.
286. Cut a red 16AWG stranded core wire to 65 mm and strip both ends to 8 mm. On one end, crimp a 16AWG ferrule connector.


287. Crimp the free end of the 65 mm wire and the free end of the wire from Step 286 together
with a twin ferrule connector as shown.

288. Route the wire to the black DIN rail terminal blocks and secure in place as shown.

289. Cut 4 black 16AWG wires to 72 in. On two of the wires, apply green heat shrink 2 in. from the ends. On the other two wires, apply blue heat shrink 2 in. from the ends as seen below.
290. Take one of the blue wires from Step 289 and strip both ends to 8 mm. Crimp a 16AWG ferrule connector on one end, and an (M4)#8 fork connector on the other.

291. Insert the side with the ferrule connector into the last open black DIN rail terminal block as shown. Route the black wire through the bottom channel and through the wire gland on the front left side of the box so that it hangs outside of the box.
292. Now strip the bottom red wire of the other fuse line to 8 mm as shown below.
293. Take one of the green wires from Step 289 and strip both ends to 8 mm. Crimp a red butt connector on one end and an (M4)#8 fork connector on the other.

294. Crimp the free end of the wire in Step 292 into the red butt connector as shown. Route this wire through the bottom cable tray and through the wire gland to the outside of the box, similar to Step 291.
295. Now take the remaining blue and green wires from Step 289 and strip both ends of each wire to 8 mm. On both ends of the green wire, crimp (M4)#8 fork connectors. On one end of the blue wire, crimp an (M4)#8 fork connector, and on the other end crimp a quick connector.
296. Connect the quick connect from the blue wire into the bottom A1 port on the Definite Purpose Contactor as shown below. Route the cable through the channel below the contactor and through the wire gland to the outside of the box, similar to Step 291.

297. Connect one of the red fork connectors on the green wire to the L port on the 48V PSU. Route the cable through the cable trays and then through the wire gland to the outside of the box, similar to Step 291.
298. There should now be four cables going through the wire gland, as shown below.
299. Grab the emergency stop and disassemble it by loosening the four screws on top.

300. Take the bottom half (black portion) of the E-Stop and set vertically so that the skinnier side is facing up. Place a socket attachment from the screwdriver kit on top of the circular port as shown.
301. Using a hammer, use a single strike to the socket as shown below. This should knock out the vent cover and leave an empty hole.
302. Insert the ends of the four cables from Step 298 through the hole created in the previous step, as shown below.

303. Insert the fork connectors into the E-Stop’s ports as shown. Note, in order to put the lid back on, you may need to bend the fork connectors so that they fit within the casing.
304. Cut a black 16AWG stranded core wire to 9 in. and strip both ends to 8 mm. Crimp an (M4)#8 fork connector on one end and a quick connector on the other as shown.
305. Plug the quick connect from this cable into the other A1 port on the Contactor. Route the other end of the cable through the cable tray below it and to the L port on the VFD, as shown.

306. Use electrical tape to tape the four wires coming from the E-Stop together up the whole length of the wires, all the way to the wire gland. Tape should be placed about every 5-6 inches.
307. Acquire shielded spindle cable and cut to 7 in. Strip one end to 60 mm, removing the foil, yellow wire, and filler textile material. Strip the ends of the red, white, and black wires to 8 mm and crimp 16AWG ferrule connectors to produce the result seen below.
308. Apply heat shrink around the stranded shielding cable from the spindle cable as shown.

309. Acquire a 5-port terminal block and secure the red, white, and black wires into it exactly as shown.


310. Cut two green 16AWG wires, one to 9 in. and one to 65 mm. Strip both ends of each wire to 8 mm. On the 9 in. wire, crimp a 16AWG ferrule connector onto one end as shown.
311. Crimp a 16AWG twin ferrule connector onto the 65 mm green wire and exposed portion of the stranded shielding cable from Step 299. Secure the twin ferrule connector into the 5-port terminal block as shown.
312. Crimp a 16AWG twin ferrule connector onto the free end of the 65 mm green wire and the free end of the 9 in. green wire. Secure this twin connector into the final slot of the 5-port terminal block as shown. Slide black heat shrink over the shielded cable from the other side of the wire and position as shown, applying heat to set it in place.

313. On the other side of the shielded spindle cable, strip to 60 mm. Remove the foil, stranded shielding cable, yellow wire, and filler textile such that all that remains is the red, white, and black wires. Strip the red, white, and black wires to 8 mm. Crimp 16AWG ferrule connectors on all three.
314. Acquire one of the 14.25 in. wire duct covers and install it over the bottom wire duct as shown.

315. Insert the 5-port terminal block from the spindle cable through the spindle port below the IEC receptacles as shown. Note that the spindle cable should just rest on top of the wire duct cover. Once the terminal is in place, slide the slide cover down over the terminal block to lock in place.
316. Slide the wire duct over about 2 in. and route the long green cable from the spindle cable’s terminal block to the bus bar and secure as shown. Move duct back in place after securing.

317. On the other end of the spindle cable, secure the ferrule connectors into the Definite Purpose Contactor following the instructions below:
a. Black → T1
b. White → T2
c. Red → T3
318. Cut a red, black, and white wire each to 4 in. and strip both ends of each wire to 8 mm. Crimp a 16AWG ferrule connector onto one end of each wire, and an (M4)#8 fork connector on the other end of each wire.

319. Insert the ferrule connector side of each wire into the Definite Purpose Contactor following the instructions below. Note: It may be necessary to extend screw driver length as shown to access the terminals on this side.
a. Black → L1
b. White → L2
c. Red → L3
320. Insert the fork connectors from the other ends of these three wires into the VFD following the instructions below: Note: it may be necessary to remove the green wire to access the W port. If so, make sure to plug it back in afterwards.
a. Black → U
b. White → V
c. Red → W


321. Find the black ground cable coming out of the X-axis drive’s signal side that was left
unplugged from an earlier step. Route this cable through the cable trays and to the ground port on
the Teensy 4.1 as shown.

322. On the 48V PSU, flip the red switch from 230 to 115 as shown.

323. Acquire two fuses as shown below.
324. Open the fuse boxes as shown. Install the fuses into the boxes by pressing the fuses as far as possible. Once they have been completely installed, close the lids.


ETHERNET PORT INSTRUCTIONS HERE:
325. Layout your Ethernet MagJack, bare circuit board, ribbon cable assembly, 2 header pins, and a capacitor. DIY soldering is required.
326. Solder the Ethernet MagJack onto the bare circuit board.

327. Solder the header pin onto the circuit board.
328. Solder the Capacitor onto the circuit board
329. Cut the extra wire from the capacitor.
330. Your Ethernet Port is finished and the results should look as below.

331. Solder the remaining header pins to the Teensy 4.1
332. Now that the ethernet port and the teensy are soldered, we will install it into the machine. These are the parts needed for the installation.

333. Insert the ethernet port into the housing as shown and connect the cable into the header pins.
334. Use a M5*12 blot and appropriate nut to connect the ethernet port to the electrical box
335. Insert the Teensy 4.1 into its board in the electrical box. Orient the teensy so that number 33 aligns with the 33 on the board and plug in the cable into the header pins.

336. The finished ethernet Teensy 4.1 connection should look like this:
337. The electrical box is now complete. Optionally, you can add the wire duct covers over the wire channels, or it can be left without them.

Now the cables for connecting the machine will be created.

338. Cut three 4-core wires to 6 ft.
339. Strip one end of all three 4-core wires to 40 mm. Leave the stranded shielding on this side and attach five 22 AWG ferrule connectors. Apply heat shrink to the stranded shielding. Repeat this for all three 6 ft wires.

340. Attach a male 5-pin terminal block as shown below. Repeat for all three 6 ft wires.
341. Strip the opposite end of each 6 ft wire to 40 mm. Remove the foil and stranded shielding from this side. Crimp 22 AWG ferrule connectors to each wire.
342. Attach the male 4-pin terminal block provided with the Nema 23 stepper motor to all three 6 ft wires. The motor cables are now complete.
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

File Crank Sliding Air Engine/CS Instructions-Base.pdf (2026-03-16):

## Desktop CNC Milling Machine: Cutting Crank-Slider BASE I: General Guidelines


GENERAL SAFETY AND OPERATIONAL INSTRUCTIONS – READ BEFORE USE:

- Users must demonstrate proper personal protective equipment (PPE) use before performing work on this machine.
- Users must wear appropriate PPE (safety glasses, ear protection and mask when necessary) when operating this machine.
- NEVER operate the machine tool without all safety mechanisms (enclosure, door switch, emergency stop, limit switches) connected, complete, and fully operational.
- NEVER BYPASS ANY SAFETY EQUIPMENT.
- NEVER place hands, head, or other body parts inside the machine tool enclosure while spindle is powered and door switch / emergency stop are disengaged.
- NEVER handle sharp tools in the spindle without the emergency stop engaged.
- During ANY milling operation, if the cutting tool shows excessive wear or excessive chip build up, or if the spindle’s RPM changes noticeably (this is often audible), quickly feed hold or emergency stop the machine (depending on severity) to inspect and determine if it is safe to continue.
- Always allow the spindle to reach its target speed before entering a cut.
- Always double-check setup steps and part programming to minimize machine accidents.
- Always watch and listen to EVERY milling operation closely. Keep a hand resting over the emergency stop button: quick reactions are necessary in mitigating damage to the machine and tools.

## II: Operator Checklist

### Operator name: ______________________________________

### Workpiece:__________________________________________

### Date:_______________________________________________

### For each tool while running the program

OP10 | OP20
- | | Check position as the tool approaches the part

### Before running the program

OP10 | OP20
- | | Program has been simulated in CAM
- | | All tool offsets are set per the setup sheet
- | | Workpiece is clamped in the proper position
- | | Correct program is selected on the machine
| | Work offsets are set for:
- | | X axis
- | | Y axis
- | | Z axis

## III. Part Programming (Autodesk Fusion) OP10

1. Start Fusion and open the provided file. Select the open option from the drop-down menu in the top left corner of Fusion. Select Open from my computer… in the following prompt. Find Base Assembly.f3z and select upload.


2. After uploading the file, three parts and an assembly will be in the folder on the left-hand side of the program. Open the Base Assembly file.


3. From the drop-down menu, select the Manufacture tab. In browser, drop down Models then drop down Base Assembly v1:1 and hide Vice Assembly v1:2. Ensure your view cube and assembly are oriented as shown.
4. To begin toolpath generation, create a new Setup. From the Orientation drop-down menu, select X & Y axes Select the back edge outlined in red for the X Axis.

5. After selecting the X axis, select the Y axis as the perpendicular edge outlined in red.
6. Select Selected point under the Origin drop-down menu. Select the point on the bottom of the vise outlined in blue. Check Flip X Axis.

7. Select Model and choose Body1 under Part base v1:1.
8. Under the Stock tab, select From solid for the stock mode. Chose Body1 under Stock base v1:1 then press OK.


9. Hide the Sketches under Base Assembly v1:1. Hide the component Stock base v1:1. To hide components and sketches select the eye outlined in red.
10. Slowly double click Setup1 and rename to OP10. Next select 2D Adaptive Clearing and select 1/4" flat endmill within the library. Set Preset to Delrin Contour Roughing.
1 | 2

3

4

11. Select the Geometry tab and for pocket selections select the outer edge of the part outlined in blue. Ensure that the red arrow is outside of the part and in the correct direction as shown below.


12. Select the Heights tab and for the Bottom Height Drop down select Selection. Select the bottom surface highlighted in dark blue. For the Offset box, enter -0.1 in. The front view should match the last figure.


13. Under the Passes tab, enter 0.075 in for the Optimal Load. Ensure the Direction is set to Climb and Radial Stock to Leave is set to 0.01 in. Axial Stock to Leave should be set to zero. Select OK when finished.
14. Under the Linking tab, setMaxiumum Stay-Down Distance to 2 in, Stay-Down Level to 50%, and Horizontal and Vertical LeadIn/out Radius to 0.01 in. Press OK.

15. Right click the 2D Adaptive Clearing tool path that was just created. Select Create Derived Operation > 2D Milling > 2D Contour. Select the Delrin Contour Finishing preset.
16. Select Face and ensure the same tool is selected. For the Feed & Speed preset, use Delrin Facing. Under the Passes tab, set the Direction to Climb. Select OK when finished.

17. OP10 should be finished at this point. Right click on OP10 and select Simulate. Under Colorization choose Comparison. Press the play button at the bottom center of the window. Adjust the Accuracy slider until simulation runs smoothly. Once the simulation is complete, the part should be green if programmed correctly. Note: If Accuracy is set to the lowest value, blue may appear around the part.

## Part Programming (Autodesk Fusion) OP20


18. Unhide Sketches under Base Assembly v1: 1. Hide Vise Assembly v1:1 and unhide Vise Assembly v1:2 to begin programming OP20. Create a new setup. Ensure that your view block and assembly are oriented in the correct direction.
19. For Orientation select X & Y axes and choose the back edge for X outlined in blue. Select the perpendicular edge like OP10 outlined in green. Check Flip X Axis. For Model select Body1 under Part base v1:1.

20. Select Selected point under the Origin drop-down menu. Select the point on the bottom of the vise boxed in red.
21. Under the Stock Tab ensure the Mode is set to From preceding setup. Check Continue Rest Machining. Rename this setup to OP20.

22. Create a Face operation. Ensure the same 1/4” flat endmill is selected. Choose the Delrin Contour Finishing preset. Under the Passes tab, set the Direction to Climb.
23. Create a 2D Adaptive Clearing operation. Ensure the same tool is selected. Select the Delrin Contour Roughing preset.

24. Under the Geometry tab select the black sketch line around the top edge of the part outlined in blue. Right click on Closed Chain 1 and select Flip Directions so that the tool path follows the outside edge.
25. Hide the Sketches under Base Assembly v1:1. Note: If the sketch isn’t hidden at this step the selection of the height in the next step will not work properly
26. Under the Heights tab set the bottom height to the floor of the part shown in blue.

27. Under the Passes tab, set the Optimal Load to 0.055 in. Turn Stock to Leave on and set Radial Stock to Leave and Axial Stock to 0.005.
28. Under the Linking tab, set Maximum Stay-Down Distance to 0.2 in, Stay Down Level to 50%, Horizontal and Vertical LeadIn/out Radius to 0.01 in. Press OK.

29. Create a 2D Adaptive Clearing operation. Ensure the same tool is selected. Select the Delrin Contour Roughing preset.


30. Under the Geometry tab select the floor of the part shown in blue. Unhide Sketches in Base Assembly v1:1.


31. Select the Stock Contours box and select the black line on the sketch then hide the sketch again. The stock contour should be shown in yellow.
32. Under the Passes tab, set the Optimal Load to 0.055 in. Turn Stock to Leave on and set Radial Stock to Leave to 0.01 in and Axial Stock to Leave to 0.005 in. Press OK.

33. Under the Linking tab, set Maximum Stay-Down Distance to 0.2 in, Stay Down Level to 50%, Horizontal and Vertical LeadIn/out Radius to 0.01 in. Press OK.
34. Right click the 2D Adaptive Clearing tool path that was just created. Select Create Derived Operation > 2D Milling > 2D Contour. Select the Delrin Contour Finishing preset.

35. Under the Passes tab, turn off Stock to Leave. Under the Linking tab, set Horizontal Lead-In Radius to zero, Linear Lead-In Distance to 0.1 in, and change the Ramp Type to Plunge. Ensure Ramp and Radial Clearance Height are 0.1 and 0 in respectively. Press OK.
36. Create a 2D Contour toolpath. Make sure the 1/4" flat endmill is selected and set Preset to Delrin Contour Finishing.

37. In browser, unhide Sketches under Base Assembly v1:1. Under Geometry, select the sketch outlining the outer geometry of the Base as shown. If the red arrow is on the inside of the geometry, right-click on the selection and click Flip directions.
38. In the Heights tab, change the Bottom Height to Selection. Select the face shown below. In the Passes tab, ensure that Stock to Leave is turned off. Press OK.

39. OP20 should now be finished. Hide Sketches in Base Assembly v1:1. Right click on OP20 and select Simulate. Under Colorization choose Comparison. Press the play button at the bottom center of the window. Adjust the Accuracy slider until simulation runs smoothly. Once the simulation is complete, the part should be green if programmed correctly. Note: If Accuracy is set to the lowest value, blue may appear around the part.


## IV: Setup and Probing

OP10

1. Place the base stock centered on the vice jaws on 1 1/8” parallels. The stock should be resting with the widest face down on the parallels and the longest edge along the X-axis as seen below.


2. Use a 6mm Allen key to tighten the bolt in the center of the front vise jaw (if it is a different vise style, follow manufacturer instructions to clamp the part). This should close on the part and clamp tightly. As you tighten the vise, apply force down on the part. This will make sure that the part is evenly seated on the parallels. Check this by gently shaking the parallel; if it shakes noticeably against the part, try again
(NOTE: an uneven surface may not seat perfectly against a flat parallel).
3. Gather the probe and attach the probing tip. Slide the probe into the spindle with a ¼” collet and tighten by hand. This should hold the probe safely. Be sure that the spindle is powered off by the emergency stop or door switch.


4. With the electrical box on and connected to both the computer and machine tool, plug the probe into the electrical box and GENTLY displace the probe tip. The light should change from green to red and the computer software should show a “P” alarm while the probe tip senses contact. Both conditions must be met to ensure probe operation.


5. Carefully jog the probe over the part. Do not allow the probe tip to touch any surface while jogging, as excessive force or deflection can permanently damage the probe tip. Carefully jog the probe until it is as centered as visually possible over the part and 5-7 mm from the top surface of the part.

6. Before probing, reduce the rapids rate to 25%. Rapid movement rate can be changed with the minus sign buttons in the “Rapids” section shown below. This is an important step. This is done so that any errors in probing can be safely caught before any damage is done.
NOTE: If using a different version of ioSender, there may be a “slider” instead of buttons. Slide bar to approximately 25% rapid rate.


7. Move to the “Probing” tab in the ioSender software. From there, move to the “Center finder” option.

8. Ensure that the “Action” is set to “Set coordinate system” in G54. Uncheck the “Lock” box. Measure the stock and type in the workpiece dimensions in millimeters. This should be roughly 92mm in the X-direction and 40mm in the Y-direction, but stock sizes may differ. Select the external option. Select the external bore option for probing the outside surfaces of the stock.

(external)

9. In the “Probing clearances” section, set the probing depth. This value will determine how far down the probe travels to touch the workpiece. It is equal to the distance between the current probe tip position and the place on the part that will be probed-- it may be necessary to roughly measure this distance before probing to ensure correct positioning and mitigate errors.


10. Double check inputs. Errors are much more difficult to catch quickly in operation. Press “Start” and watch the probing cycle very closely. Emergency-stop the machine if anything unexpected occurs and safely try again. The machine should move across the part to touch each side once. This will set the X and Y offsets for a coordinate system centered on the rectangular block. The X- and Y- offsets should be zeroed (this is sometimes displayed on ioSender with ±0.001”).


11. We will now set the Z height for the coordinate system. This is based on the surface of the X-carriage and will include the tool offset. Jog the probe safely away from the part and remove it from the spindle.
12. Gently replace the probe tip with the probe touch plate. Insert the shaft of the probe into the holder on the left side of the vise. If the signal cable was disconnected, plug it into the probe and test again to be sure the signal is working.


13. Never handle tools in the enclosure while the spindle is powered.

Insert the ¼” endmill into the spindle and secure tightly using the provided wrenches. The tool should protrude just past the start of the tool shank.


14. Jog the tool so that there are no obstructions between the tool and touch probe. Move back to the “Probing” tab and select “Tool length offset”. Check the “Probe fixture @ G59.3 with tool” box, uncheck the “Establish reference offset” box, check the “Set coordinate system or offset” box, and set the touch plate height to 92.44 mm (or the otherwise determined accurate distance from the touch plate to the X-carriage surface). Then set the probing distance to 100 mm.

15. Double check all parameters and press start. The tool should slowly approach the touch plate and gently press it twice. This will set the Z-coordinate at the bottom of the vise / top of the X-carriage.
16. Remove the probe completely from the enclosure. If the machine tool is not equipped with compressed air, slide the plastic chip fan onto the spindle over the tool as seen below.

17. Jog the tool so that it starts the operation above the part.

The machine tool should now be ready to run the first operation.

REVIEW AND FOLLOW GENERAL INSTRUCTIONS AND CHECKLIST.

Be ready to feed hold the machine IMMEDIATELY after pressing cycle start. This will allow the spindle to reach the desired speed before milling begins (this usually takes no longer than 5 seconds – the spindle should be making a constant sound and not “ramping up”).
ALWAYS ALLOW THE SPINDLE TO GET UP TO SPEED BEFORE ENTERING A CUT.

After pressing feed hold and letting the spindle reach its target RPM, you can resume the operation with cycle start.

18. Watch the entire operation carefully.

OP20

19. Once OP10 is complete, jog the tool out of the way. Stop the machine and open the door. Clear any chips as necessary. Carefully slide the chip fan off the spindle. Remove the ¼” endmill with the wrenches.
20. Use the Allen key to loosen the vise jaw and remove the cut part. It may be necessary to clean up edges with a file or deburring tool.


21. Replace the part upside down, on the same parallels, and clamp down on the newly cut surface in the same orientation as before.
22. Follow steps 5-15 to probe the part and ¼” tool. The X- and Y- measurements for stock probing remain the same. For this setup, ensure that the probing depth is set so that the flat faces of the stock contact the probe tip and not the probe shaft while probing.
23. Repeat steps 16 and 17.

24. Watch the entire operation carefully.

25. Once OP20 is complete, jog the tool out of the way. Emergency stop the machine and open the door. Clear any chips as necessary. Carefully slide the chip fan off the spindle. Remove the ¼” endmill with the wrenches.
26. Use the Allen key to loosen the vise jaw and remove the cut part.


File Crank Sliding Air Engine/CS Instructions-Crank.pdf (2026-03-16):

## LC-CNC Crank-Slider: Crank I: General Guidelines

GENERAL SAFETY AND OPERATIONAL INSTRUCTIONS – READ BEFORE USE:

- Users must demonstrate proper personal protective equipment (PPE) use before performing work on this machine.
- Users must wear appropriate PPE (safety glasses, ear protection and mask when necessary) when operating this machine.
- NEVER operate the machine tool without all safety mechanisms (enclosure, door switch, emergency stop, limit switches) connected, complete, and fully operational.
- NEVER BYPASS ANY SAFETY EQUIPMENT.
- NEVER place hands, head, or other body parts inside the machine tool enclosure while spindle is powered and door switch / emergency stop are disengaged.
- NEVER handle sharp tools in the spindle without the emergency stop engaged.
- During ANY milling operation, if the cutting tool shows excessive wear or excessive chip build up, or if the spindle’s RPM changes noticeably (this is often audible), quickly feed hold or emergency stop the machine (depending on severity) to inspect and determine if it is safe to continue.
- Always allow the spindle to reach its target speed before entering a cut.
- Always double-check setup steps and part programming to minimize machine accidents.
- Always watch and listen to EVERY milling operation closely. Keep a hand resting over the emergency stop button: quick reactions are necessary in mitigating damage to the machine and tools.

## II: Operator Checklist

### Operator name: ______________________________________

### Workpiece:__________________________________________

### Date:_______________________________________________

### For each tool while running the program

OP10 | OP20
- | | Check position as the tool approaches the part

### Before running the program

OP10 | OP20
- | | Program has been simulated in CAM
- | | All tool offsets are set per the setup sheet
- | | Workpiece is clamped in the proper position
- | | Correct program is selected on the machine
| | Work offsets are set for:
- | | X axis
- | | Y axis
- | | Z axis

## III. Part Programming (Autodesk Fusion) OP10

1. Start Fusion and open the provided file. Select the open option from the drop-down menu in the top left corner of Fusion. Select Open from my computer… in the following prompt. Find Crank Assembly.f3z and select upload.


2. After uploading the file, multiple parts and an assembly will appear on the left-hand side. Open the Cut crank file.

3. From the drop-down menu, select the Manufacture tab


4. In BROWSER, drop down Models then Cut crank v1:1. With these dropped, Hide Origin, Stock crank v1:1, Vise Assembly v1:2, Soft Jaw V2 v1:1 and v1:2. To hide components and sketches select the eye outlined in red.

5. Underneath the Milling tab, click on the Setup dropdown menu. Select New Setup.


6. From the Orientation drop-down menu, select X and Y axes. Select the horizontal edge of the vice assembly highlighted.
7. After Selecting the X axis, select the perpendicular edge for the Y axis and check off the Flip Y Axis box.

8. Under the Origin drop-down menu, select Selected point. Select the point on the bottom of the part outlined in blue.
9. Next, in Model, click on Select. Now in BROWSER, drop down Part crank v1:1>Bodies and click on Body1. Confirm your assembly and view cube are oriented as shown.

10. Under the Stock tab, select From solid for the mode. Choose Body1 under Stock crank v1:1. Then, press the OK button. Setup1 is complete

11. Rename Setup1 as OP10 by slowly double clicking the name. Next, click on the 2D dropdown menu and select the 2D Adaptive Clearing tool option.

12. In the tool tab, select the 1/8” tool and the Aluminum roughing 2 preset.


13. Next, click on the geometry tab click on the outer edge on the bottom of the part as shown in the figure below.

14. Next, click on the heights tab. For the retract height, select highest of… for from and select top for stock, model, and fixture. For the top height, select highest of… for from and select top for stock and ignore for model and fixture. For the bottom height, select selection for from and choose the face as shown in the figure below.


15. In the passes tab, check the multiple depths tab and change the maximum roughing stepdown to 0.205 in. Then, change the optimal load to 0.015 in, the direction to climb, the radial stock to leave to 0.005 in, and the axial stock to leave to 0 in.

16. In the linking tab, change the maximum stay-down distance to 2 in, the stay-down level to most, and leads & transitions to 0.01 in. Then click ok.

17. Select the 2D Adaptive Clearing tool from the 2D dropdown menu.
18. Select the 1/8” tool and Aluminum roughing 3 preset.

19. Next, move on to the geometry tab and check the stock contours box. For the pocket selections, select the larger radius below the cylinder on the part. For the stock selections, select the outer edge of the bottom face of the part.
20. In the heights tab, for the retract height select highest of… for from, then top for stock, model and fixture. For the top height, select highest of… for from, then top for stock and ignore for model and fixture. For the bottom height, select selection for from then select the top face of the part as shown in the figure below.


21. In the passes tab, change the radial and axial stock to leave to 0.005 in.

22. In the linking tab, change the maximum stay-down distance to 2 in, the stay-down level to most, and the leads & transitions to 0.01 in. Then click ok.

23. Select the 2D Adaptive Clearing tool from the 2D dropdown menu.
24. Select the 1/8” tool and Aluminum roughing 4 preset.
25. In the geometry tab, check the stock contours box. For pocket selections, select the 8 open pockets at the top of the part. For stock selections select the outer edge at the bottom of the part.

26. In the heights tab, for the retract height select highest of… for from, then select top for stock, model and fixture. For the top height, select highest of… for from, then select top for the stock and ignore for model and fixture. For the bottom height, select selection for from, then select the face as shown in the figure below.

27. In the passes tab, change the optimal load to 0.015 in and the radial and axial stock to leave to 0.005 in.

28. In the linking tab, change the maximum stay-down distance to 2 in, the stay-down level to most, and the leads & transitions to 0.01 in. Then click ok.

29. Select the 2D Adaptive Clearing tool, then select the 1/8” tool and Aluminum roughing 1 preset.

30. In the geometry tab, check the stock contours box. For pocket selections, choose the inner radius (highlighted in the lighter shade of blue) at the bottom of the cylinder as shown in the figure below. For the stock selections, choose the outer radius (highlighted in orange) of the cylinder as shown in the figure below.


31. In the heights tab, for the retract height select the highest of… for from, then top for stock, model and fixture. For the top height, select highest of… for from, then top for stock and ignore for model and fixture. For the bottom height select selection for from, then select the face around the cylinder as shown in the figure below.

32. In the passes tab, change the optimal load to 0.015 in then change the radial and axial stock to leave to 0.005 in.

33. In the linking tab, change the maximum stay-down distance to 2 in, the stay-down level to most and the leads & transitions to 0.01 in. Then click ok.

34. Select the 2D Face tool, then select the 1/8” tool and Aluminum facing preset.


35. In the geometry tab, select the edge as shown in the figure below highlighted in orange.

36. Next, in the heights tab, for the retract height select highest of… for from, then top for stock, model and fixture. For the top height, select highest of… for from, then top for stock and ignore for model and fixture. For the bottom height select highest of… for from, then ignore for stock and fixture and top for model.

37. In the passes tab, change the direction to climb. Then click ok.

38. Select the 2D contour tool, then select the 1/8” tool and the Aluminum contour roughing preset.
39. In the geometry tab, select the bottom edge of the cylinder as shown in the figure below.

40. In the heights tab, for the retract height select highest of… for from, then top for stock, model and fixture. For the top height select highest of… for from, then top for stock and ignore for model and fixture. For the bottom height select selection for from and select the face surrounding the cylinder as shown in the figure below. Then click ok.
41. Select 2D Pocket tool from the 2D dropdown menu. Make sure the 1/8” tool and Aluminum pocket roughing preset are selected.

42. In the geometry tab, check the stock contours box. For pocket selections, select the edge (highlighted in blue with dots at the end) as shown in the figure below. For stock selections, select the bottom edge of the part as shown in the figure (highlighted in orange).


43. In the heights tab, for the retract height select highest of… for from, then top for stock, model and fixture. For the top height, select highest of… for from then top for stock and ignore for model and fixture. For the bottom height, select selection for from, then select the face as shown in the figure below.

44. In the passes tab, uncheck the stock to leave box. Then click ok.

45. Select the 2D Pocket tool again in the 2D dropdown menu. Then make sure the 1/8” tool and Aluminum pocket roughing preset are selected.


46. In the geometry tab, for pocket selections, select the 8 pockets as shown in the figure below. Make sure that you select the inner edge of these pockets.
47. In the heights tab, for the retract height select highest of… for from, the top for stock, model and fixture. For the top height, select highest of… for from, then top for stock and ignore for model and fixture. For the bottom height, select selection for from then select the face as shown in the figure below.

48. In the passes tab, uncheck the stock to leave box. Then click ok.

49. Select the 2D Bore tool in the 2D dropdown menu. Make sure the 1/8” tool and the Aluminum boring preset are selected.

50. In the geometry tab, select the inner face of the hole as shown in the figure below. Zoom and pan as much as you need.
51. In the heights tab, for the retract height select highest of… for from, then top for stock, model and fixture. For the bottom height, select selection for from the select the bottom face of the part as shown in the figure below. Change the offset to 0.15 in.


52. In the passes tab, check the stock to leave box and change the radial stock to leave to -0.00425 in. Then click ok.

53. Select 2D Bore tool again in the 2D dropdown menu. Make sure the 1/8” tool and Aluminum boring preset are selected.

54. In the geometry tab, select the inner face of the hole (highlighted in blue) as shown in the figure below.

55. In the heights tab, for the retract height select highest of… for from, then top for stock, model and fixture. For the top height change the offset to -0.1 in. For the bottom height, select selection for from, then the bottom face of the part as shown in the figure below and change the offset to -0.02 in.


56. In the passes tab, check the stock to leave box then change the radial stock to leave to -0.00425 in. Then click ok.
57. OP10 should now be finished. Hide Sketches in Base Assembly v1:1. Right click on OP10 and select Simulate. Under Colorization choose Comparison. Press the play button at the bottom center of the window. Adjust the Accuracy slider until simulation runs smoothly. Once the simulation is complete, the part should be green if programmed correctly. Note: If Accuracy is set to the lowest value, blue may appear around the part.


## Part Programming (Autodesk Fusion) OP20

1. OP10 is now complete. Make sure you are in the Manufacture workspace.
2. Make sure Vise Assembly v1:2 is visible. Hide sketches, stock crank v1:1 and Vise Assembly v1:1. Make sure the entire assembly is oriented as shown.
3. Create OP20 by selecting New Setup.

4. Set the orientation to Z axis/plane & X axis. Then select the edge shown for the Z axis and check the Flip Z Axis box.

5. For X axis, select the edge shown in the figure.


6. For the origin, click selected point. Turn on sketches and pick the point below the part.

7. For the model, drop down part crank v1:1, drop down bodies, then select Body 1.
8. In the stock tab select from preceding setup and then check the continue rest machining box.

9. Once you have completed your set up rename it to OP20 by selecting the setup then selecting it again, then you can rename it.
10. You may have realized that your components have disappeared. If this happens, click on the name of your file under models, then select show all components. Then hide all the components mentioned in step 2.

11. Select the 2D Adaptive Clearing tool option. Make sure the 1/4” tool and Aluminum Roughing preset are selected.


12. In the geometry tab, select the edge selected below. You will have to click the red arrow to make the selection look as is in the figure.

13. In the heights tab, for retract height select highest of… for from then top for stock, model and fixture. For top height select highest of for from then top for stock, ignore for model and fixture. For bottom height select selection for from, then click the top face of the part as shown in the figure below.


14. In the passes tab change the optimal load to 0.015 in, the radial stock to leave to 0.1 in and the axial stock to leave to 0.01 in.

15. In the linking tab, change the maximum stay-down distance to 2 in, the stay-down level to most, and leads & transitions to 0.01 in.

16. Select the 2D Face tool option, then make sure you select the ¼” tool and the Aluminum facing 1 preset.
17. In the geometry tab, select the chain tab then select closed chain for mode and choose the edge selected in the figure below.

18. In the heights tab, for the retract height select highest of… for from then select top for stock, model, and fixture. For the top height select highest of… for from then select top for stock and ignore for model and fixture. For the bottom height select selection for from and then choose the top face of the part.


19. In the passes tab, change the pass extension to 0.13 in, the stock offset to 0.125 in and the direction to climb. Check the multiple depths and stock to leave boxes. Change the maximum stepdown to 0.025 in and the axial stock to leave to 0.01 in. Then click ok.

20. Select the 2D Adaptive Clearing tool option, make sure the tool is set to the ¼” tool and the preset is set to Aluminum roughing.


21. In the geometry tab, select the edge shown in the figure below.
22. In the heights tab, for the retract height select highest of… for from, then top for the stock, model and fixture. For the top height select highest of.. for from, then top for stock and ignore for model and fixture. For the bottom height select selection, then select the face as shown in the figure (you may need to hide the soft jaws the reach this face) and change the offset to -0.03 in.

23. In the passes tab, change the optimal load to 0.015 in, then axial and radial stock to leave to 0.01 in.

24. In the linking tab, change the maximum stay-down distance to 2 in, the stay-down level to most, and leads & transitions to 0.01 in. Then click ok.
25. Select the 2D contour tool option, make sure the ¼” tool and Aluminum contour roughing preset are selected.

26. In the geometry tab, select the chain tab, choose the closed chain mode and then select the face as shown in the figure.

27. In the heights tab, for the retract height select highest of… for from then top for stock, model, and fixture. For the top height select highest of… for from, then top for stock and ignore for model and fixture. For the bottom height select selection for from then select the face as shown in the figure (you may need to hide the soft jaws to select this edge) and set the offset to -0.025 in.


28. In the passes tab, check the stock to leave box and change the radial stock to leave to 0.005 in and the axial stock to leave to 0 in. Then click ok.
29. Select the 2D Face tool option, make sure the ¼” tool and Aluminum finishing preset are selected.

30. In the geometry tab, select the outer edge of the top face of the part as shown in the figure below.

31. In the heights tab, for the retract height select highest of… for from, then select top for stock, model and fixture. For the top height select highest of… for from then top for stock, then ignore for model and fixture. For the bottom height select selection for from and select the top face of the part as shown in the figure below.

32. In the passes tab change the direction to climb. Then click ok.


33. OP20 should now be finished. Hide Sketches in Base Assembly v1:1. Right click on OP20 and select Simulate. Under Colorization choose Comparison. Press the play button at the bottom center of the window. Adjust the Accuracy slider until simulation runs smoothly. Once the simulation is complete, the part should be green if programmed correctly. Note: If Accuracy is set to the lowest value, blue may appear around the part.

## IV: Setup and Probing

1. Place the crank stock centered on 1 1/8” parallels. The stock should be resting with the widest face down on the parallels and the flatter, rolled edge along the X-axis as seen below. Close the jaws but do not tighten.
2. Use a 6mm Allen key to tighten the bolt in the center of the front vise jaw (if it is a different vise style, follow manufacturer instructions to clamp the part). This should close on the part and clamp tightly. As you tighten the vise, apply force down on the part. This will make sure that the part is evenly seated on the parallels. Check this by gently shaking the parallel; if it shakes noticeably against the part, try again (NOTE: an uneven surface may not seat perfectly against a flat parallel).
3. Gather the probe and attach the probing tip. Slide the probe into the spindle with a ¼” collet and tighten by hand. This should hold the probe safely. Be sure that the spindle is turned off by the emergency stop or door switch.


4. With the electrical box on and connected to both the computer and machine tool, plug the probe into the electrical box and GENTLY move the probe tip. The light should change from green to red and the computer software should show a “P” alarm while the probe tip senses contact. Both conditions must be met to ensure probe operation.

5. Carefully jog the probe over the part. Do not allow the probe tip to touch any surface while jogging, as excessive force or deflection can permanently damage the probe tip. Carefully jog the probe until it is as centered as visually possible over the part and 5-7 mm from the top surface of the part.
6. Before probing, reduce the rapids rate to 25%. Rapid movement rate can be changed with the minus sign buttons in the “Rapids” section shown below.
NOTE: this is an important step. This is done so that any errors in probing can be safely caught before any damage is done.


7. Move to the “Probing” tab in the ioSender software. From there, move to the “Center finder” option.
8. Ensure that the “Action” is set to “Set coordinate system” in G54. Uncheck the “Lock” box. Measure the stock and type in the workpiece dimensions in millimeters. This should be roughly 92mm in the X-direction and 40mm in the Y-direction. Select the external option. Select the external bore option for probing the outside surfaces of the stock.
9. In the “Probing clearances” section, set the probing depth. This value will determine how far down the probe travels to touch the workpiece. It is equal to the distance between the current probe tip position and the place on the part that will be probed-- it may be necessary to roughly measure this distance before probing to ensure correct positioning and mitigate errors.


10. Double check inputs. Errors are much more difficult to catch quickly in operation. Press “Start” and watch the probing cycle very closely. Emergency stop the machine if anything unexpected occurs and safely try again. The machine should move across the part to touch each side once. This will set the X and Y offsets for a coordinate system centered on the rectangular block. The X- and Y- offsets should be zeroed.
11. We will now set the Z height for the coordinate system. This is based on the surface of the X-carriage and will include the tool offset. Jog the probe safely away from the part and remove it from the spindle.

12. Gently replace the probe tip with the probe touch plate. Insert the shaft of the probe into the holder on the left side of the vise. If the signal cable was disconnected, plug it into the probe and test again to be sure the signal is working.
13. Press the emergency stop. Never handle tools in the spindle without the emergency stop engaged.

Fully unscrew the collet from the spindle. Gently press out the ¼” collet and replace with a 1/8” collet. Press until the collet “clicks” into place and is correctly seated.

Screw the collet onto the spindle loosely, then insert the 1/8” endmill into the spindle and secure tightly using the provided wrenches. The tool should protrude just past the start of the flutes.


14. NOTE: Trying to jog any axis while the emergency stop is engaged will move the coordinate system without moving the machine. Do not jog until the emergency stop is disengaged.

Carefully jog the spindle until the tool rests approximately 5mm above and centered on the touch plate.

15. Move back to the “Probing” tab and select “Tool length offset”. Check the “Add offset” box and set the touch plate height to 92.44 mm (or the otherwise determined accurate distance from the touch plate to the X-carriage surface – see Troubleshooting).
16. Double check all parameters and press start. The tool should slowly approach the touch plate and gently press it twice. This will set the Z-coordinate at the bottom of the vise / top of the X-carriage.
17. Jog the tool out of the way and remove the probe completely from the enclosure. If the machine tool is not equipped with compressed air, slide the plastic chip fan onto the spindle over the tool as seen below.

18. Jog the tool so that it starts the operation above the part.

The machine tool should now be ready to run the first operation.

REVIEW AND FOLLOW GENERAL INSTRUCTIONS AND CHECKLIST.

Be ready to feed hold the machine IMMEDIATELY after pressing cycle start. This will allow the spindle to reach the desired speed before milling begins (this usually takes no longer than 5 seconds – the spindle should be making a constant sound and not “ramping up”).
ALWAYS ALLOW THE SPINDLE TO GET UP TO SPEED BEFORE ENTERING A CUT.

After pressing feed hold and letting the spindle reach its target RPM, you can resume the operation with cycle start.

19. Watch the entire operation carefully.

OP20

20. Once OP10 is complete, jog the tool out of the way. Emergency stop the machine and open the door. Clear any chips as necessary. Carefully slide the chip fan off the spindle. Remove the 1/8” endmill with the wrenches.
21. Use the Allen key to loosen the vise jaw and remove the cut part.
22. Place one aluminum soft jaw on each vise face, with the patterned side facing up and towards the other jaw (see below).
23. Place the crank part centered on the geometry of the aluminum soft jaws. The part should rest naturally centered and flat between the soft jaws. Close the jaws but do not tighten.
24. To prevent the jaws from moving when clamping a part (and because this vise has no threaded holes), place an appropriate plastic spacer between the soft jaw faces at the bottom of the jaws. The spacer should be about the same width as the gap in between the jaw faces, but loose enough to move.
25. Use a 6mm Allen key to tighten the bolt in the center of the front vise jaw (if it is a different vise style, follow manufacturer instructions to clamp the part). This should close on the part and clamp tightly. As you tighten the vise, apply force down on the part. This will make sure that the part is evenly seated on the parallels. Check this by gently shaking the parallel; if it shakes noticeably against the part, try again (NOTE: an uneven surface may not seat perfectly against a flat parallel).

Check by hand to see if the part and spacer are tightly held. If the part is loose and the spacer is tight, choose a spacer of slightly smaller width. If the part is tight but the jaws have moved from flat against the jaw face, choose a slightly wider spacer. DO NOT attempt to run parts without good spacing and flat jaws: this could damage parts, tools, and the machine.

26. Press the emergency stop. Never handle tools in the spindle without the emergency stop engaged.

Fully unscrew the collet from the spindle. Gently press out the 1/8” collet and replace with a 1/4” collet. Press until the collet “clicks” into place and is correctly seated.

27. Follow steps 3-10 to probe the part. The X- and Y- measurements should remain the same as in probing the first operation. For this setup, ensure that the probing depth is set so that the flat faces of the stock contact the probe tip and not the probe shaft while probing.
28. Press the emergency stop. Never handle tools in the spindle without the emergency stop engaged.

Insert the ¼” endmill into the spindle and secure tightly using the provided wrenches. The tool should protrude just past the start of the flutes.

29. Follow steps 11-16 to set the Z-offset.
30. Repeat step 18.
31. Watch the entire operation carefully.
32. Once OP20 is complete, jog the tool out of the way. Emergency stop the machine and open the door. Clear any chips as necessary. Carefully slide the chip fan off the spindle. Remove the 1/4” endmill with the wrenches.
33. Use the Allen key to loosen the vise jaw and remove the cut part.

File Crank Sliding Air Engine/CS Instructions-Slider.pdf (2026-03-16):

1

## Desktop CNC Milling Machine: Cutting Crank-Slider SLIDER I: General Guidelines

GENERAL SAFETY AND OPERATIONAL INSTRUCTIONS – READ BEFORE USE:

- Users must demonstrate proper personal protective equipment (PPE) use before performing work on this machine.
- Users must wear appropriate PPE (safety glasses, ear protection and mask when necessary) when operating this machine.
- NEVER operate the machine tool without all safety mechanisms (enclosure, door switch, emergency stop, limit switches) connected, complete, and fully operational.
- NEVER BYPASS ANY SAFETY EQUIPMENT.
- NEVER place hands, head, or other body parts inside the machine tool enclosure while spindle is powered and door switch / emergency stop are disengaged.
- NEVER handle sharp tools in the spindle without the emergency stop engaged.
- During ANY milling operation, if the cutting tool shows excessive wear or excessive chip build up, or if the spindle’s RPM changes noticeably (this is often audible), quickly feed hold or emergency stop the machine (depending on severity) to inspect and determine if it is safe to continue.
- Always allow the spindle to reach its target speed before entering a cut.
- Always double-check setup steps and part programming to minimize machine accidents.
- Always watch and listen to EVERY milling operation closely. Keep a hand resting over the emergency stop button: quick reactions are necessary in mitigating damage to the machine and tools.

2

## II: Operator Checklist

### Operator name: ______________________________________

### Workpiece:__________________________________________

### Date:_______________________________________________

### For each tool while running the program

OP10 | OP20
- | | Check position as the tool approaches the part

### Before running the program

OP10 | OP20
- | | Program has been simulated in CAM
- | | All tool offsets are set per the setup sheet
- | | Workpiece is clamped in the proper position
- | | Correct program is selected on the machine
| | Work offsets are set for:
- | | X axis
- | | Y axis
- | | Z axis


3

## III. Part Programming (Autodesk Fusion)

1. Start Fusion and open the provided file. Select the open option from the drop-down menu in the top left corner of Fusion. Select Open from my computer ... in the following prompt. Locate Slider.f3z and select upload.
2. After uploading the file, three parts and an assembly will be in the folder on the left-hand side of the program. Open the Slider Assembly file.

4

3. From the drop-down menu, select the Manufacture tab to begin toolpath generation.
4. Hide the sketches under Slider Assembly v1:1. Hide the component Stock slider v1:1. Hide Vise Assembly v1:2. To hide components and sketches select the eye outlined in red. Ensure your view cube and assembly are oriented as shown.

### Commented [TW1]: Need to hide vise assembly v1:2 Commented [TW2]: Add initial view of assembly

Commented [TW3R2]: Fix the tree menu

Commented [TW4R2]: Hide relationships

### Commented [TW5R2]: Update hiding of assembly to one button

5. Create a new setup.; Commented [TW7]: Choose a better edge

6. From the Orientation drop-down menu, select Z axis/plane & X axis. Rotate the assembly and select the back edge outlined in red for the Z axis. Check the Flip Z Axis box.

### Commented [TW6]: Put “go to manufacuture tab”

before the hiding of the views. Decouple step 4.


6

7. After selecting the Z axis, select the X axis as the horizontal edge outlined in red. Check the Flip X Axis box.
8. Select “Selected point” under the Origin drop-down menu. Select the point on the bottom of the vise outlined in red. You may need to make sketches visible.

7

9. Select Model and choose Body1 under Part slider v1:1.

8

10. Under the Stock tab, select From solid for the stock mode. Chose Body1 under Stock slider v1:1 . Then click OK.

9

11. Once you have clicked OK you may have noticed that your part slider is the only body that appears in your software. Right click on Slider Assembly v1:1 and select Show All Components. Once that is done, repeat Step 3.

### Commented [TW8]: Make figures larger so we can read


10

11

12. Slowly double click Setup1 and rename to OP10. Next select 2D Face and select the 0.25-inch diameter tool
within the library. Make sure Aluminum facing preset is selected. | Commented [TW9]: Should say “Aluminum facing”


12

13. In Retract Height, change from clearance height to Highest of… and select the top option. In Top Height, select from highest of and choose top for stock and ignore for model and fixture. In Bottom Height, choose selection and pick the top face of the part.
14. Finally, select climb for direction in the Passes tab and click ok.

13

15. Under 2D, select 2D-Adaptive clearing, and make sure the ¼’’ is selected. Change the preset to Aluminum Contour Roughing. In geometry tab, select the top of the slider for pocket selections.

14

15

16. Switch Retract height and Top height to Highest of. Change the Bottom height to selection and select the bottom right face, zoom in as needed to select it. Change the offset to -0.05 in.
17. Under the Passes tab, change the optimal load to 0.012 in, radial stock to leave and axial stock to leave to 0.005 in and make sure stock to leave is checked.


16

18. In the linking tab, change the maximum stay-down to 2 in, and choose 50% stay-down level. Then, change the leads and transitions to 0.01 in. Then click ok.
19. Next, select 2D- Contour. Make sure the same ¼’’ tool is selected. Change the preset to Aluminum Finishing.

17

20. Under Geometry tab, select the contour of the slider’s base.
21. Under heights, change the retract height and top height to the highest of. Then switch to selection in bottom height and select the face on the top right of the slider. Zoom in if needed. Also, set an offset of -0.04 in. Then click ok

18

22. OP10 should be finished at this point. Right click on OP10 and select Simulate. Under Colorization choose Comparison. Press the play button at the bottom center of the window. Adjust the Accuracy slider until simulation runs smoothly. Once the simulation is complete, the part should be green if programmed correctly. Note: If Accuracy is set to the lowest value, blue may appear around the part.


19

23. After finishing OP10, click on the view button of the vise assembly v1:2, and click on setup and new setup to make the CAM for OP20. Ensure your view cube and assembly are oriented as shown.
24. Change the orientation to Z axis/plane and X axis and select the edge highlighted in blue on the vise.

20

25. For the x axis, select edge highlighted in blue on the vise on the bottom. Then change the origin to the selected point option and click on the blue dot on the base. You should turn sketches on to select the point for the origin.
26. For the model, choose Body 1 under Part slider v1:1, bodies.

21

27. In the stocks tab, check the continue rest machining tab. Then click ok.
28. Again, you may have noticed that your part slider is the only body that appears in your software. Repeat step
10. But hide Vise Assembly v1:1 instead of Vise Assembly v1:2.


22

29. Double click on the setup to change the name to OP20.


23

30. Select 2D-Adaptive Clearing. Select 1/8’’ tool.
31. Under geometry, select the contour of the base of the cylinder that appears highlighted in the image.

24

32. Change the Retract Height and Top Height to highest of… Change bottom height to selection and choose the top left side of the slider
33. In the passes tab, change the optimal load to 0.015 in. Check the multiple depths and change the maximum roughing stepdown to 0.155 in. Modify the radial stock and axial stock to 0.005 in.


25

34. Change the maximum stay-down Distance to 2 in, and the leads and transitions to 0.01in. Then, click ok.
35. Select 2D- Face. Select the 1/8’’ tool. Then select Aluminum facing.


26

36. In the geometry tab, select the contour of the cylinder as shown in the picture.
37. In the passes tab, change the stock offset to 0.05in, the stepover to 0.1 in and direction to climb. Then check multiple depths and change the maximum stepdown to 0.02in. Finally check the stock to leave and change the axial stock to leave to 0.02in. Click ok.

27

38. Create another Facing step. Keep the Aluminum facing preset.
39. Click in the geometry tab and select face contours. A pop-up menu appears, select the top face of the cylinder marked in blue, and make sure all loops option and start outside option are selected.
40. In the passes tab, change the stock offset to 0.05in, the stepover to 0.1 in and the direction to climb. Then, click ok.


28

### 41. Add a 2D-Contour. Double check we are using the same tool. Choose the Aluminum

contour roughing preset.

42. In geometry, select the perimeter of the base in the small cylinder as highlighted in the image.

29

43. In the passes tab, check roughing passes. Change the stepover to 0.005in. Then, change the maximum stepover to 0.0125 in. Then select ok.
44. Add a 2D- Pocket. Select the Aluminum pocket roughing preset. In the geometry tab, select the perimeter of the outer cylinder as highlighted in blue in the image.

30

45. Under heights tab, bottom height, change from option to selection and select the top left surface as shown in the image.
46. In passes, uncheck stock to leave option. Then click ok.


31

47. Add a 2D-adaptive clearing step. Select the Aluminum contour finishing preset. In geometry, select chain, then in mode select open chain. Orbit around the piece to select the U shape edge as shown in the image. Then, orbit back to select the opposite edge as shown in the image.


32

33

48. In heights, change the retract height and top height to highest of. For bottom height, switch from option to selection and select the highlighted bottom reference as shown in image. Orbit and zoom as needed.
49. In passes, change the optimal load to 0.01in and uncheck the stock to leave option.

34

50. In linking, change the maximum stay-down distance to 2 in and the leads and transitions to 0.01in. Then click ok.

35

51. OP20 should now be finished. Hide Sketches in Base Assembly v1:1. Right click on OP20 and select Simulate. Under Colorization choose Comparison. Press the play button at the bottom center of the window. Adjust the Accuracy slider until simulation runs smoothly. Once the simulation is complete, the part should be green if programmed correctly. Note: If Accuracy is set to the lowest value, blue may appear around the part.


36


37

## IV: Setup and Probing

1. Place one aluminum soft jaw on each vise face, with the “ridge” side facing up and towards the other jaw (see below).
2. Place the slider stock centered on the inner ridge of the aluminum soft jaws. The stock should be resting with the widest face down on the parallels and the longest edge along the X-axis as seen below. Close the jaws but do not tighten.


38

3. To prevent the jaws from moving when clamping a part (and because this vise has no threaded holes), place an appropriate plastic spacer between the soft jaw faces at the bottom of the jaws. The spacer should be about the same width as the gap in between the jaw faces, but loose enough to slide in. This spacer is?? FIX FOR NEW SJ
4. Use a 6mm Allen key to tighten the bolt in the center of the front vise jaw (if it is a different vise style, follow manufacturer instructions to clamp the part). This should close on the part and clamp tightly. As you tighten the vise, gently apply force down on the part. This will make sure that the part is evenly seated on the jaws (NOTE: an uneven surface may not seat perfectly on a flatter surface).

Check by hand to see if the part and spacer are tightly held. If the part is loose and the spacer is tight, choose a spacer of slightly smaller width. If the part is tight but the jaws have moved from flat against the jaw face, choose a slightly wider spacer. DO NOT attempt to run parts without good spacing and flat jaws: this could damage parts, tools, and the machine.

39

5. Gather the probe and attach the probing tip. Slide the probe into the spindle with a ¼” collet and tighten by hand. This should hold the probe safely. Be sure that the spindle is turned off by the emergency stop or door switch.
6. With the electrical box on and connected to both the computer and machine tool, plug the probe into the electrical box and GENTLY move the probe tip. The light should change from green to red and the computer software should show a “P” alarm while the probe tip senses contact. Both conditions must be met to ensure probe operation.


40

7. Carefully jog the probe over the part. Do not allow the probe tip to touch any surface while jogging, as excessive force or deflection can permanently damage the probe tip. Carefully jog the probe until it is as centered as visually possible over the part and 5-7 mm from the top surface of the part.
8. Before probing, reduce the rapids rate to 25%. Rapid movement rate can be changed with the minus sign buttons in the “Rapids” section shown below.

41

NOTE: this is an important step. This is done so that any errors in probing can be safely caught before any damage is done.

9. Move to the “Probing” tab in the ioSender software. From there, move to the “Center finder” option.
10. Ensure that the “Action” is set to “Set coordinate system” in G54. Uncheck the “Lock” box. Measure the stock and type in the workpiece dimensions in millimeters. This should be roughly 28mm in the X-direction and 16mm in the Y-direction. Select the external option. Select the external bore option for probing the outside surfaces of the stock.

(external)

42

11. In the “Probing clearances” section, set the probing depth. This value will determine how far down the probe travels to touch the workpiece. It is equal to the distance between the current probe tip position and the place on the part that will be probed-- it may be necessary to roughly measure this distance before probing to ensure correct positioning and mitigate errors.


43

12. Double check inputs. Errors can be costly and are much more difficult to catch quickly in operation. Press “Start” and watch the probing cycle very closely. Emergency stop the machine if anything unexpected occurs and safely try again. The machine should move across the part to touch each side once. This will set the X and Y offsets for a coordinate system centered on the rectangular block. The X- and Y- offsets should be zeroed.
13. We will now set the Z height for the coordinate system. This is based on the surface of the X-carriage and will include the tool offset. Jog the probe safely away from the part and remove it from the spindle.

44

14. Gently replace the probe tip with the probe touch plate. Insert the shaft of the probe into the holder on the left side of the vise. If the signal cable was disconnected, plug it into the probe and test again to be sure the signal is working.
15. Press the emergency stop. Never handle tools in the spindle without the emergency stop engaged.

Insert the ¼” endmill into the spindle and secure tightly using the provided wrenches. The tool should be held just above the flutes.

16. NOTE: Trying to jog any axis while the emergency stop is engaged will move the coordinate system without moving the machine. Do not jog until the emergency stop is disengaged.

45

Carefully jog the spindle until the tool rests approximately 5mm above and centered on the touch plate.

17. Move back to the “Probing” tab and select “Tool length offset”. Check the “Add offset” box and set the touch plate height to 92.44 mm (or the otherwise determined accurate distance from the touch plate to the X-carriage surface – see Troubleshooting).
18. Double check all parameters and press start. The tool should slowly approach the touch plate and gently press it twice. This will set the Z-coordinate at the bottom of the vise / top of the X-carriage.


46

19. Jog the tool out of the way and remove the probe completely from the enclosure. If the machine tool is not equipped with compressed air, slide the plastic chip fan onto the spindle over the tool as seen below.
20. Remove all tools or obstacles from the enclosure and replace the door.

47

21. Jog the tool so that it starts the operation above the part.

The machine tool should now be ready to run the first operation.

REVIEW AND FOLLOW GENERAL INSTRUCTIONS AND CHECKLIST.

Be ready to feed hold the machine IMMEDIATELY after pressing cycle start. This will allow the spindle to reach the desired speed before milling begins (this usually takes no longer than 5 seconds – the spindle should be making a constant sound and not “ramping up”).
ALWAYS ALLOW THE SPINDLE TO GET UP TO SPEED BEFORE ENTERING A CUT.

After pressing feed hold and letting the spindle reach its target RPM, you can resume the operation with cycle start.

22. Watch the entire operation carefully.

48

OP20

23. Once OP10 is complete, jog the tool out of the way. Emergency stop the machine and open the door. Clear any chips as necessary. Carefully slide the chip fan off the spindle. Remove the ¼” endmill with the wrenches.
24. Use the Allen key to loosen the vise jaw and remove the cut part.
25. Replace the part upside down, on the same soft jaws. You will clamp down on the newly cut surface in the same orientation as before.
26. Repeat steps 1-,4 with a new spacer. In this example, a ZZZmm spacer was used.


49

27. Follow steps 5-21 to probe the part. The X- and Y- measurements should remain the same. For this setup, ensure that the probing depth is set so that the flat faces of the stock contact the probe tip and not the probe shaft while probing.
28. Press the emergency stop. Never handle tools in the spindle without the emergency stop engaged.

Fully unscrew the collet from the spindle. Gently press out the ¼” collet and replace with a 1/8” collet. Press until the collet “clicks” into place and is correctly seated.

## INCORRECT

50

29. Screw the collet onto the spindle loosely, then insert the 1/8” endmill into the spindle and secure tightly using the provided wrenches. The tool should protrude just past the start of the flutes.
30. Repeat steps X-X with the new tool.
31. Repeat step X.


51

32. Watch the entire operation carefully.

52

33. Once OP20 is complete, jog the tool out of the way. Emergency stop the machine and open the door. Clear any chips as necessary. Carefully slide the chip fan off the spindle. Remove the 1/8” endmill with the wrenches.
34. Use the Allen key to loosen the vise jaw and remove the cut part.

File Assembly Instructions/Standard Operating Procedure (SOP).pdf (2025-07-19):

## Desktop CNC Milling Machine: Standard Operating Procedure I: General Guidelines

GENERAL SAFETY AND OPERATIONAL INSTRUCTIONS:

- Never operate the machine tool without all safety mechanisms (enclosure, door switch, emergency stop, limit switches) connected, complete, and fully operational.
- Never place hands, head, or other body parts inside the machine tool enclosure while spindle is powered and door switch / emergency stop are disengaged.
- Never handle sharp tools in the spindle without the emergency stop engaged.
- Always watch and listen to EVERY milling operation closely. Keep a hand resting over the emergency stop button: quick reactions are necessary in mitigating damage to the machine and tools.
- During ANY milling operation, if the cutting tool shows excessive wear or excessive chip build up, or if the spindle’s RPM changes noticeably (this is often audible), quickly feed hold or emergency stop the machine (depending on severity) to inspect and determine if it is safe to continue.
- Always allow the spindle to reach its target speed before entering a cut.
- Always double-check setup steps and part programming to minimize machine accidents.
- Jogging any axis while the emergency stop is engaged will offset a probed coordinate system.

## II. Part Programming (Autodesk Fusion)

The following instructions are based on the programming for a simple machining test that will validate machine tool performance after construction. The part stock is a 36 x 36 x 20mm block, 3D Printed in ABS plastic with 100% infill. This part will be safer to cut than metals as a first machining test. This method of coordinate placement should be used for every part, however.
NOTE: This section of the SOP is geared toward machine validation and new part programming. Students should not have to place coordinates in this way when programming parts for the crank-slider demonstrator.
1. Start Fusion and open a new design. Save the file and name it.


2. Ensure that the vise and square demo part are uploaded to Fusion. Select “Insert Component” and choose the “Vise” file.


3. Orient the vise so that it is flat on the X-Y plane (any orientation on the planes will work, however, as the rest of the program will be built relative to the vise). Press “OK”.
4. Insert the “Demo part” as a component. Using the sliders or number inputs, orient the part on the X-Y plane like the vise. Because this part is symmetrical, any face can be parallel to the vise jaw. The part should always be oriented in the way it will be placed in the vise for cutting.

5. We will now use joints to finish orienting the parts. Select “Joint” from the top ribbon.


6. Join the part so that it rests on the “parallels” modeled on the vise. This is managed by selecting a coincident point on coincident faces of each component as seen below.


The result is shown below.

7. Create a new sketch on the bottom of the vise.

8. The demo part should have a center point sketch. If this is not visible, be sure that sketch visibility is enabled for this component. Use the project tool to project this point onto the bottom of the vise.
9. Change to the “Manufacture” workspace in Fusion.


10. Once in the “Manufacture” workspace, create a new setup with the “Setup” button under “Milling”.
11. In the “Setup” tab, select the demo part for “Model”.

12. Under “WCS” and “Orientation”, select “Z axis/plane & X axis”.

Choose an ‘up and down’ edge of the vise for the Z-axis and an edge across the vise jaw for the X-axis. If necessary, select “Flip Z Axis” to make the Z-axis point upward.

13. In the drop-down menu for “Origin”, choose “Selected point”.

Select the point we sketched at the bottom of the vise. Again, sketch visibility must be enabled.


(36mm)

The result is shown below.

14. Move to the “Stock” tab. Choose “Fixed size box”. The dimensions of this stock, as mentioned, are 36x36x20mm. Be sure to input the correct units, as measured values may differ from active document units.

The result is shown below. The part is ready for milling tool paths.


The following instructions are not related to coordinate placement and simply serve to complete the programming and manufacture of the square plastic demo part.

15. Create a 2D adaptive toolpath and select the bottom edge of the small square for “Geometry”.
16. In the “Tool” tab, select the 1/4” flat endmill from the vise tool library. Change the spindle speed to 5500 rpm and the cutting feedrate to 32 in/min.


17. In the “Heights” tab, move to “Bottom Height” and change to “Selection”. Select the top face of the diamond as the bottom as seen.
18. In the “Passes” tab, set the optimal load to 0.04 in. Turn off “Stock to Leave”.

NOTE: These cutting parameters are for ABS plastic ONLY. Do NOT attempt to cut metal parts with these parameters.


19. Copy and paste the toolpath, then change the geometry to the bottom edge of the diamond as seen below.
20. In the “Heights” tab, change the bottom surface selection to the bottom surface of the diamond as seen below.

21. Simulate the entire operation to be sure that no errors were made in programming.


The part is ready for milling.

## III: Setup and Probing

Due to the nature of this machine and the software used to run it, all toolpaths must be programmed with the Z-coordinate placed at the bottom of the vise (the top surface of the X-carriage). This will be covered in steps 1-13. The following steps show how to hold and probe a workpiece for milling operations.

22. Place the material stock in the center of the vice jaws on top of the necessary parallels. In the following pictures, a 36 x 36 x 20mm plastic block is placed on 1-1/4” parallels. This procedure will work for probing any rectangular block.


23. Use a 6mm Allen key to tighten the bolt in the center of the front vise jaw (if it is a different vise style, follow manufacturer instructions to clamp the part). This should close on the part and clamp tightly. As you tighten the vise, apply force down on the part. This will make sure that the part is evenly seated on the parallels. Check this by gently shaking the parallel; if it shakes noticeably against the part, try again
(NOTE: an uneven surface may not seat perfectly against a flat parallel).
In certain cases, this vise style may struggle to clamp a part – if this occurs, see Troubleshooting at the end of this document.

24. Gather the probe and attach the probing tip. Slide the probe into the spindle with a ¼” collet and tighten by hand. This should hold the probe safely. Be sure that the spindle is turned off by the emergency stop or door switch.


25. With the electrical box on and connected to both the computer and machine tool, plug the probe into the electrical box and GENTLY move the probe tip. The light should change from green to red and the computer software should show a “P” alarm while the probe tip senses contact. Both conditions must be met to ensure probe operation.


26. Carefully jog the probe over the part. Do not allow the probe tip to touch any surface while jogging, as excessive force or deflection can permanently damage the probe tip. Carefully jog the probe until it is as centered as visually possible over the part and 5-7 mm from the top surface of the part.
27. Before probing, reduce the rapids rate to 25%. Rapid movement rate can be changed with the minus sign buttons in the “Rapids” section shown below.
NOTE: this is an important step. This is done so that any errors in probing can be safely caught before any damage is done.


28. Move to the “Probing” tab in the ioSender software. From there, move to the “Center finder” option.

29. Type in the workpiece dimensions in millimeters, then select the external option. Select the external bore option for probing the outside surfaces of the stock. NOTE: The “Lock” box will need to be unchecked for a rectangular part.


30. In the “Probing clearances” section, set the probing depth. This value will determine how far down the probe travels to touch the workpiece. It is equal to the distance between the current probe tip position and the place on the part that will be probed- it may be necessary to roughly measure this distance before probing to ensure correct positioning and mitigate errors.


31. Double check inputs. Errors are much more difficult to catch quickly in operation. Press “Start” and watch the probing cycle very closely. Emergency stop the machine if anything unexpected occurs and safely try again. The machine should move across the part to touch each side once. This will set the X and Y offsets for a coordinate system centered on the rectangular block.


32. We will now set the Z height for the coordinate system. This is based on the surface of the X-carriage and will include the tool offset. Jog the probe safely away from the part and remove it from the spindle.
33. Gently replace the probe tip with the probe touch plate. Insert the shaft of the probe into the holder on the left side of the vise. If the signal cable was disconnected, plug it into the probe and test again to be sure the signal is working.


34. Press the emergency stop. Never handle sharp tools in the spindle without the emergency stop engaged.
Insert the tool into the spindle at the desired length and secure tightly using the provided wrenches. This may require replacing the collet if the tool is not the same diameter as the probe shaft. In this case, a ¼” endmill is used.


35. NOTE: Trying to jog any axis while the emergency stop is engaged will move the coordinate system without moving the machine. Do not jog until the emergency stop is disengaged.

Carefully jog the spindle until the tool rests approximately 5mm above and centered on the touch plate.


36. Move back to the “Probing” tab and select “Tool length offset”. Check the “Add offset” box and set the touch plate height to 92.44 mm (or the otherwise determined accurate distance from the touch plate to the X-carriage surface – see Troubleshooting).
37. Double check all parameters and press start. The tool should slowly approach the touch plate and gently press it twice. This will set the Z-coordinate at the bottom of the vise / top of the X-carriage.

38. Jog the tool out of the way and remove the probe completely from the enclosure. If the machine tool is not equipped with compressed air, slide the plastic chip fan onto the spindle over the tool as seen below.
39. Jog the tool so that it starts the operation above the part.
BEFORE RUNNING ANY PROGRAM THE ENDMILL MUST BE ABOVE THE PART.

Be ready to feed hold the machine IMMEDIATELY after pressing cycle start. This will allow the spindle to reach the desired speed before milling begins (this usually takes no longer than 5 seconds – the spindle should be making a constant sound and not “ramping up”).
ALWAYS ALLOW THE SPINDLE TO GET UP TO SPEED BEFORE ENTERING A CUT.

After pressing feed hold and letting the spindle reach its target RPM, you can resume the operation with cycle start.

The machine tool should now be ready to run a program.

## IV: Operator Checklist

OP10 | OP20 | Check
- | | Entire operation simulated in Fusion 360
- | | Workpiece is properly secured
- | | X and Y offsets established
- | | Tool offset established
- | | NC program is the correct version

## V: Cutting and Checking Demo Part

NOTE: Read through this entire section before starting the machining operation. Several steps require quick reactions to machine movements and familiarity with the following step.

While these parameters should work for ABS plastic, it is possible that any material (especially plastics) can “gum up” the tool when milled. Follow all safety guidelines CLOSELY.

40. A good way to double-check probed offsets on this part is with physical marks on the part. Draw two lines on the part at roughly 4mm step downs.
41. After completing steps 1-37, start and feed hold the machine to allow the spindle to get up to speed. Reduce rapids to 25% for safety. If everything is correct, resume the operation and be prepared to feed hold.
42. Feed hold the machine as it approaches the first cutting pass. The tool tip should be very close to the marked line. Do this again as it approaches its second pass.
43. Allow the machine to safely finish the operation.


44. To check machine performance, measure the machined sides of the demo part. Nominally, the smaller square is 18 mm wide, and the diamond is √648 mm (about 25.46 mm) wide. The measured values should be quite close, as seen below. The depth of each stepdown should also be measured. This value is nominally 4mm.

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

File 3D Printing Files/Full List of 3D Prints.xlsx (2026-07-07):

3D printed files and quantities
Number of Machines: | 1
Enclosure
File Name: | Quantity:
Enclosure Cover 1 | 1
Enclosure Cover 2 | 1
Corner Bracket with Magnet Top | 1
Corner Bracket for Hinge Door | 3
Corner Bracket with Magnet Bottom V2 | 1
Magnet Frame Mount | 2
CNC Mill Door Handle | 1
Connector cover top | 7
Connector cover bottom | 7
Machine
File Name: | Quantity:
X-axis Way Cover Mount | 1
Probe holder | 1
X-axis Way Cover Bed Side | 2
x hard cover | 2
Y-axis Way Cover Cover Side | 2
Y-axis Way Cover Saddle Side | 2
Y-axis Way Cover Cover Column Side | 1
Y-axis Way Cover Column Side | 1
Z-axis Way Cover Bracing Side | 1
Z-axis Way Cover Bed Side | 2
Z-Axis Limit switch mount | 1
X-axis Way Cover Motor Side | 2
X-Axis Limit switch mount | 1
Y-axis Way Cover Cover motor Side | 1
Y-axis Limit switch mount | 1
Probe touch plate | 1
Collet Fan | 1
Electrical Box
File Name: | Quantity:
DoveTailPlateFINAL | 1
SmallPlateDoveTail | 1
3PinDoveTailBracket025TEST | 1
SingleDoveTail | 1
5PinDoveTailBracket025TEST | 1
MagJackPlate | 1
PSU Side Mount 3 | 1
OptoMount5.0 | 1
FanGrills | 2
Drill and Box Prep Guides (IF BOX IS NOT PREPARED FOR YOU)
BigJig | 1
SmallJig | 1
FanHoleGuides | 1
ContactorGuide | 1

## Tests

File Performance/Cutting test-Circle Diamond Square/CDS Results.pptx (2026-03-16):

## ISO 10791-7, M1_80

Circle diamond square cutting test
- Purpose of test
  - Standardized method to evaluate positioning, contouring, and interpolation accuracy
  - Used to assess squareness, roundness, and straightness
- Machining Parameters
  - Tool: 6.35 mm 3-flute bull nose endmill with zirconium nitride coating
  - Axial depth of cut: 6 mm
  - Radial depth of cut 0.508 mm
  - Feed rate: 1200 mm/min
  - Spindle speed: 19,200 rpm

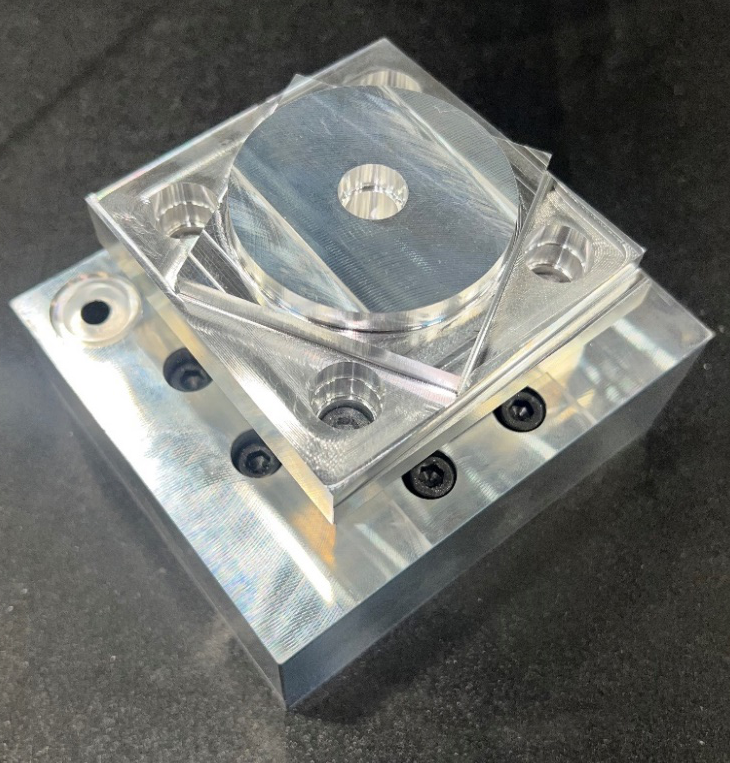
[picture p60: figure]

80 mm

80 mm

## ISO 10791-7, M1_80

Object | Characteristic | Tolerance [mm] | Desktop machine [mm] | Haas VF-4 [mm]
Central hole | Perpendicularity: C-A | 0.010 | 0.030 | 0.006
| Cylindricity: C | | 0.015 | 0.021
Square | Straightness: B | 0.005 | 0.008 | 0.002
| Straightness: F | | 0.011 | 0.004
| Straightness: G | | 0.006 | 0.003
| Straightness: H | | 0.006 | 0.002
| Perpendicularity: H-B | 0.010 | 0.041 | 0.023
| Perpendicularity: F-B | | 0.062 | 0.005
| Parallelism: G-B | | 0.021 | 0.019
Diamond | Straightness: K | 0.005 | 0.016 | 0.002
| Straightness: L | | 0.018 | 0.002
| Straightness: M | | 0.015 | 0.003
| Straightness: N | | 0.022 | 0.003
| Angularity: K-B | 0.010 | 0.023 | 0.003
| Angularity: L-B | | 0.036 | 0.007
| Angularity: M-B | | 0.026 | 0.003
| Angularity: N-B | | 0.025 | 0.004
Circle | Roundness: P | 0.015 | 0.031 | 0.010
| Concentricity: P-C | 0.025 | 0.015 | 0.002
Sloping faces | Straightness: I | 0.005 | 0.012 | 0.011
| Straightness: J | | 0.011 | 0.002
| Angularity: I-B | 0.010 | 0.014 | 0.016
| Angularity: J-B | | 0.057 | 0.007
Bored holes | Position: D1-C | 0.050 | 0.078 | 0.008
| Position: D2-C | | 0.027 | 0.003
| Position: D3-C | | 0.054 | 0.007
| Position: D4-C | | 0.037 | 0.007
| Concentricity: E1-D1 | 0.020 | 0.048 | 0.007
| Concentricity: E2-D2 | | 0.014 | 0.002
| Concentricity: E3-D3 | | 0.036 | 0.003
| Concentricity: E4-D4 | | 0.011 | 0.007

Cutting test results
- Parts measured using ZEISS Duramax coordinate measuring machine (CMM)
  - Over 10 points measured per feature
- Desktop CNC mill compared versus same cutting test on Haas VF4
- Desktop CNC mill struggled to meet ISO tolerances of 5-15 μm deviation
  - Sufficient accuracy for educational purposes
  - Average deviation of 20 μm from the Haas VF4 results

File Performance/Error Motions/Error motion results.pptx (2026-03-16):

## Error motion results

X-axis error motions: ASME B5.54

Error motion | Bidirectional error | Bidirectional repeatability | Reversal
E_(XX) | 30.0 μm | 10.5 μm | 4.8 μm
E_(YX) | 45.5 μm | N/A | N/A
E_(ZX) | 35.6 μm | N/A | N/A
E_(BX) | 194.3 μrad | 15.0 μrad | 4.5 μrad
E_(CX) | 108.9 μrad | 18.6 μrad | 2.7 μrad

## Error motion results

X-axis error motions: ASME B5.54

Error motion | Bidirectional error | Bidirectional repeatability | Reversal
E_(XX) | 30.0 μm | 10.5 μm | 4.8 μm
E_(YX) | 45.5 μm | N/A | N/A
E_(ZX) | 35.6 μm | N/A | N/A
E_(BX) | 194.3 μrad | 15.0 μrad | 4.5 μrad
E_(CX) | 108.9 μrad | 18.6 μrad | 2.7 μrad

## Error motion results

X-axis error motions: ASME B5.54

Error motion | Bidirectional error | Bidirectional repeatability | Reversal
E_(XX) | 30.0 μm | 10.5 μm | 4.8 μm
E_(YX) | 45.5 μm | N/A | N/A
E_(ZX) | 35.6 μm | N/A | N/A
E_(BX) | 194.3 μrad | 15.0 μrad | 4.5 μrad
E_(CX) | 108.9 μrad | 18.6 μrad | 2.7 μrad

## Error motion results

X-axis error motions: ASME B5.54

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

## Error motion results

X-axis error motions: ASME B5.54

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

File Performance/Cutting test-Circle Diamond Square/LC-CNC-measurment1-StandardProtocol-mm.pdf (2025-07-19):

Part name | Circle Diamond Square
Drawing number
Order number
Variant
Company
Department
CMM Type | DURAMAX
CMM No. | 120252
Operator | Master
Text

Last 1 measurements
- Approval ≠ Blocked
Part ident | 21
Time/Date | 10/25/2024 4:31 PM
Run | All Characteristics
No. measured values | 31
No. values: red | 26
Measurement Duration | 00:00:01.0

# ZEISS CALYPSO 7.6.08

Name | Measured value Nominal value | +Tol | -Tol | +/-Deviation

Central Hole

Central Hole - Perpendicularity C-A | 0.03297228 mm 0.00000000 0.01000000 0.000000000.03297228 | 0.02297228
Central Hole - Cylindricity C | 0.01774669 mm 0.00000000 0.01000000 0.000000000.01774669 | 0.00774669

Square Char

Straightness B | 0.00801080 mm 0.00000000 0.00500000 0.000000000.00801080 | 0.00301080
Straightness F | 0.00961111 mm 0.00000000 0.00500000 0.00000000 0.00961111 | 0.00461111
Straightness G | 0.00590601 mm 0.00000000 0.00500000 0.000000000.00590601 | 0.00090601
Straightness H | 0.00898795 mm 0.00000000 0.00500000 0.000000000.00898795 | 0.00398795
Perpendicularity H-B | 0.04155815 mm 0.00000000 0.01000000 0.000000000.04155815 | 0.03155815
Perpendicularity F-B | 0.06503047 mm 0.00000000 0.01000000 0.000000000.06503047 | 0.05503047
Parallelism G-B | 0.01854958 mm 0.00000000 0.00000000 0.000000000.01854958 | 0.01854958

Diamond Char

Straightness K | 0.01886505 mm 0.00000000 0.00500000 0.000000000.01886505 | 0.01386505
Straightness L | 0.01926356 mm 0.00000000 0.00500000 0.000000000.01926356 | 0.01426356
Straightness M | 0.01639938 mm 0.00000000 0.00500000 0.000000000.01639938 | 0.01139938
Straightness N | 0.01602003 mm 0.00000000 0.00500000 0.000000000.01602003 | 0.01102003
Angularity K-B | 0.02559126 mm 0.00000000 0.01000000 0.000000000.02559126 | 0.01559126
Angularity L-B | 0.03284981 mm 0.00000000 0.01000000 0.000000000.03284981 | 0.02284981
Angularity M-B | 0.02196343 mm 0.00000000 0.01000000 0.000000000.02196343 | 0.01196343
Angularity N-B | 0.03875481 mm 0.00000000 0.01000000 0.000000000.03875481 | 0.02875481
Roundness1 | 0.03642229 mm 0.00000000 0.01500000 0.000000000.03642229 | 0.02142229
Concentricity P-C | 0.02232616 mm 0.00000000 0.02500000 0.000000000.02232616

(8.4_02) StandardProtocol

Part name | Circle Diamond Square
Order number
21Part ident
Operator | Master
Time/Date | 10/25/2024 4:31 PM

# ZEISS CALYPSO

7.6.08

Name | Measured value Nominal value | +Tol | -Tol | +/-Deviation

Ramp Char

Straightness I | 0.00907625 mm 0.00000000 0.00500000 0.000000000.00907625 | 0.00407625
Straightness J | 0.01173526 mm 0.00000000 0.00500000 0.00000000 0.01173526 | 0.00673526
Angularity I-B | 0.02425792 mm 0.00000000 0.01000000 0.000000000.02425792 | 0.01425792
Angularity J-B | 0.05747553 mm 0.00000000 0.01000000 0.000000000.05747553 | 0.04747553
Position D1-C | 0.06500687 mm 0.00000000 0.05000000 0.000000000.06500687 | 0.01500687
Position D2-C | 0.01697042 mm 0.00000000 0.05000000 0.000000000.01697042
Position D3-C | 0.06661001 mm 0.00000000 0.05000000 0.000000000.06661001 | 0.01661001
Position D4-C | 0.04033213 mm 0.00000000 0.05000000 0.000000000.04033213
Concentricity E1-D1 | 0.04548879 mm 0.00000000 0.02000000 0.000000000.04548879 | 0.02548879
Concentricity E2-D2 | 0.01404691 mm 0.00000000 0.02000000 0.000000000.01404691
Concentricity E3-D3 | 0.03035340 mm 0.00000000 0.02000000 0.000000000.03035340 | 0.01035340
Concentricity E4-D4 | 0.01057414 mm 0.00000000 0.02000000 0.000000000.01057414

n.def.

Text | Event

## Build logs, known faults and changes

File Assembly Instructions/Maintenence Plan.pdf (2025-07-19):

## Desktop CNC milling machine: maintenance plan I: Daily

Before the first operation:

1. Turn on machine
- Two switches on the side of the electrical box are switched on

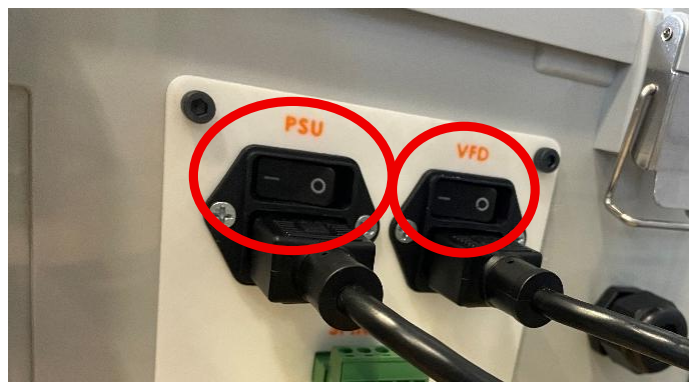
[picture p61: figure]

2. Cycle the E-Stop
- Verify the machine shuts down when pressed in and powers on when released.

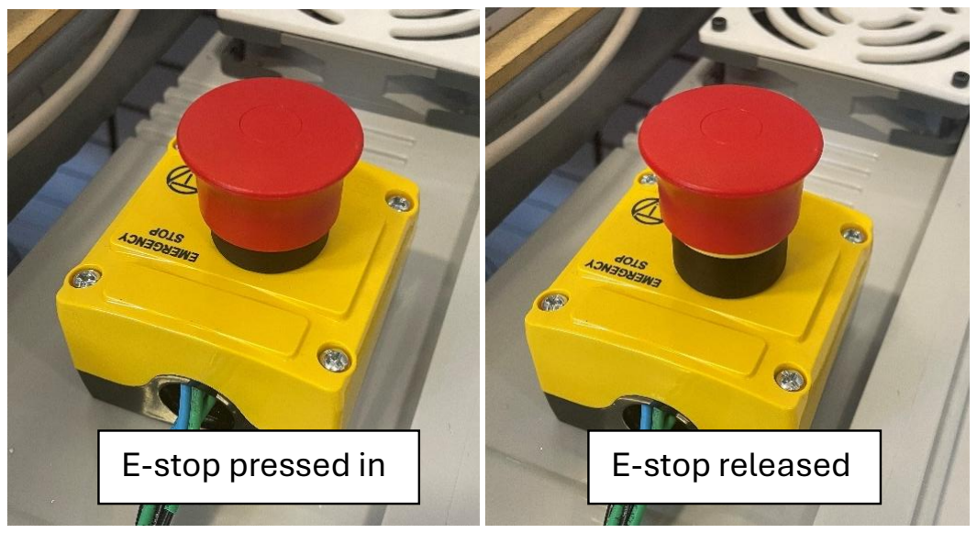
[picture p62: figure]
E-stop pressed in; E-stop released
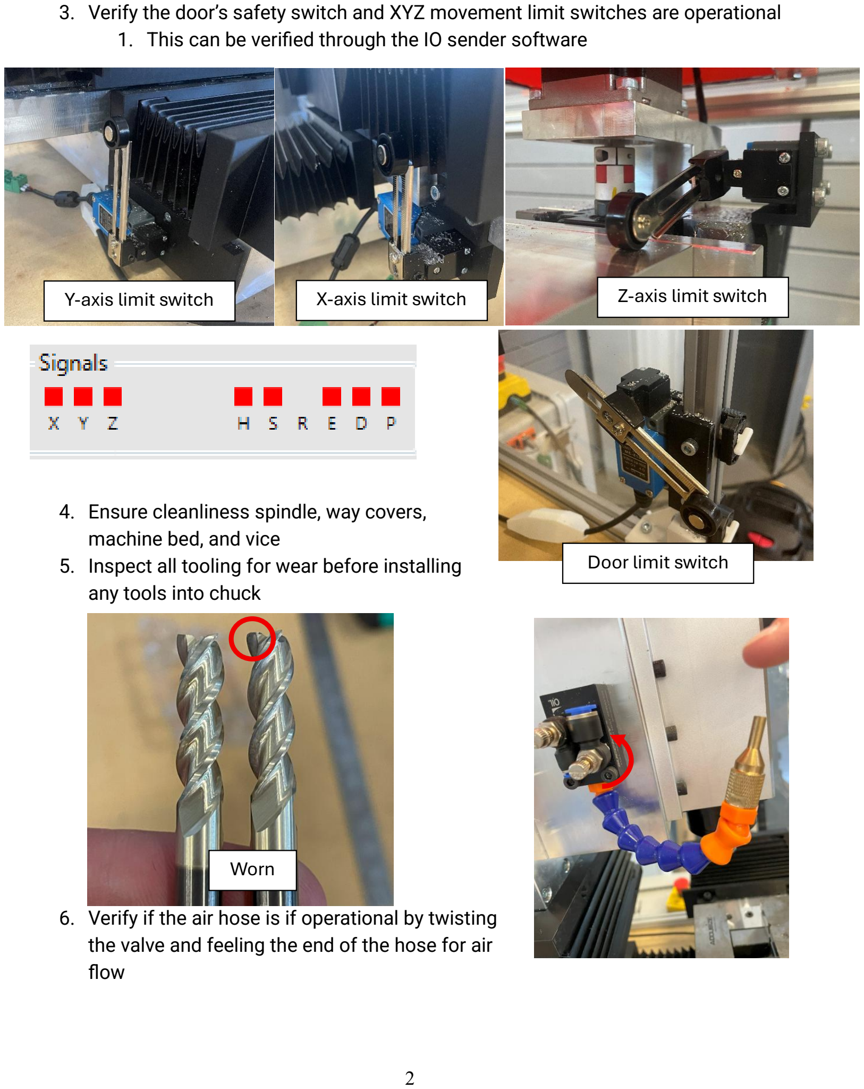
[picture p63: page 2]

3. Verify the door’s safety switch and XYZ movement limit switches are operational
1. This can be verified through the IO sender software
4. Ensure cleanliness spindle, way covers, machine bed, and vice
5. Inspect all tooling for wear before installing any tools into chuck
6. Verify if the air hose is if operational by twisting the valve and feeling the end of the hose for air flow
Y-axis limit switch | X-axis limit switch | Z-axis limit switch

### Door limit switch

### Worn

After last operation:

1. Clean all chips around the spindle, way covers, machine bed, and vice

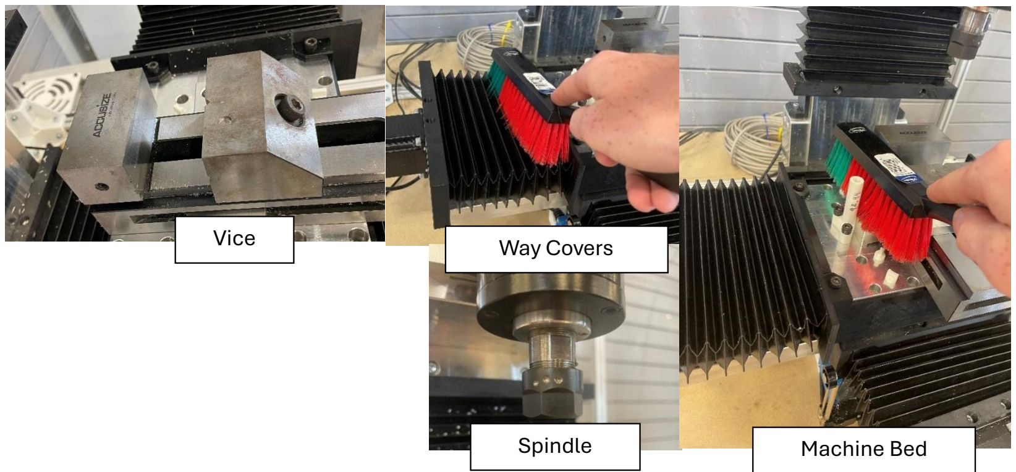
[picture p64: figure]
Vice; Way Covers; Spindle; Machine Bed

2. Power off machine

## II: Weekly

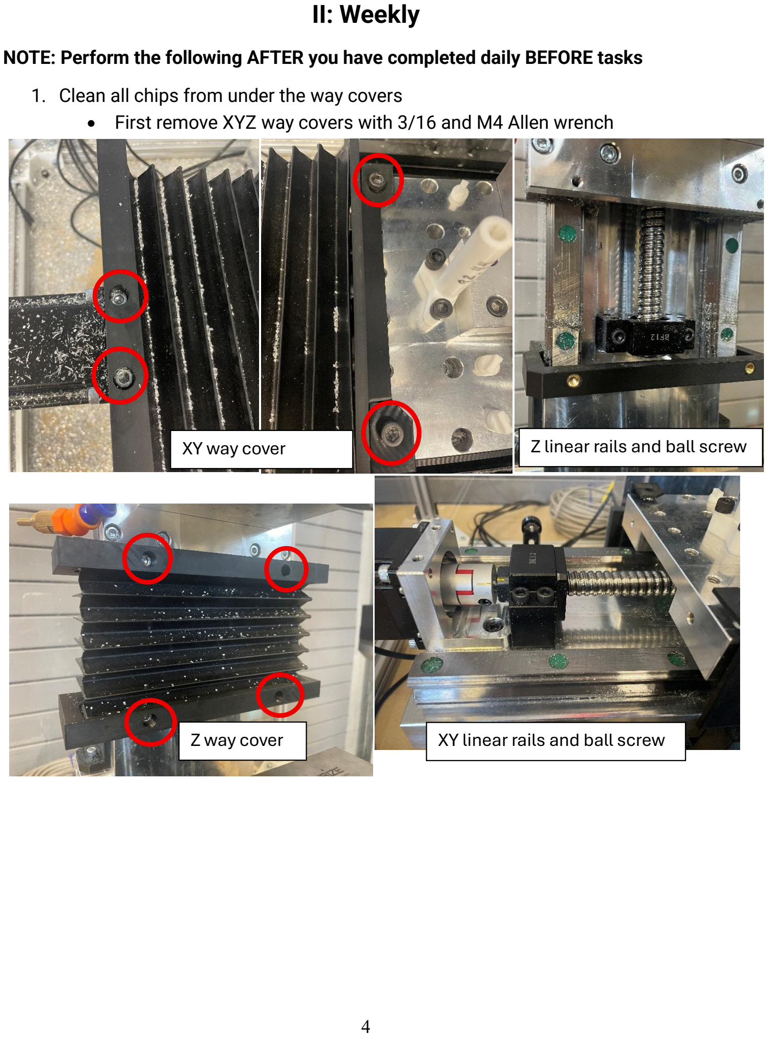
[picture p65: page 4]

NOTE: Perform the following AFTER you have completed daily BEFORE tasks

1. Clean all chips from under the way covers
- First remove XYZ way covers with 3/16 and M4 Allen wrench

### XY way cover

Z way cover | XY linear rails and ball screw

### Z linear rails and ball screw

2. With machine bed’s centered in the XY axes and way covers removed, grease all machine slide rails and ball screws
- NOTE: Wear nitrile gloves when applying grease
- Use EP1 grease provided in the BoM

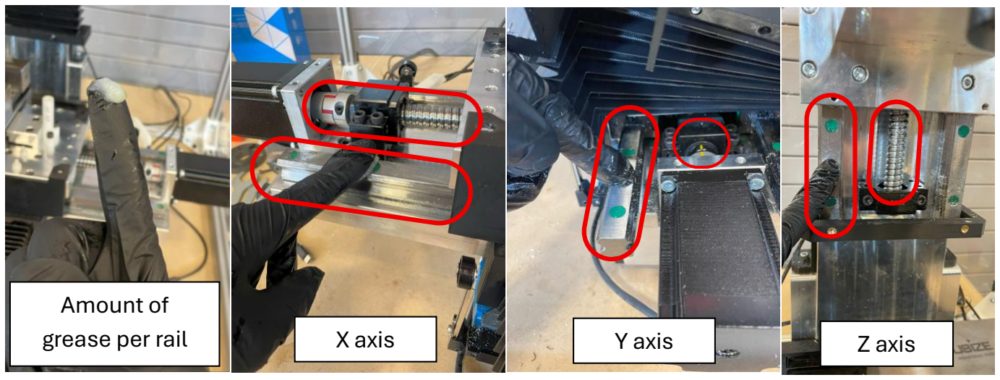
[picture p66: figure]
Amount of; grease per rail; X axis; Y axis; Z axis

3. Start the spindle warmup program for best part quality
- This program is named 09999 on the machine

## III: Monthly

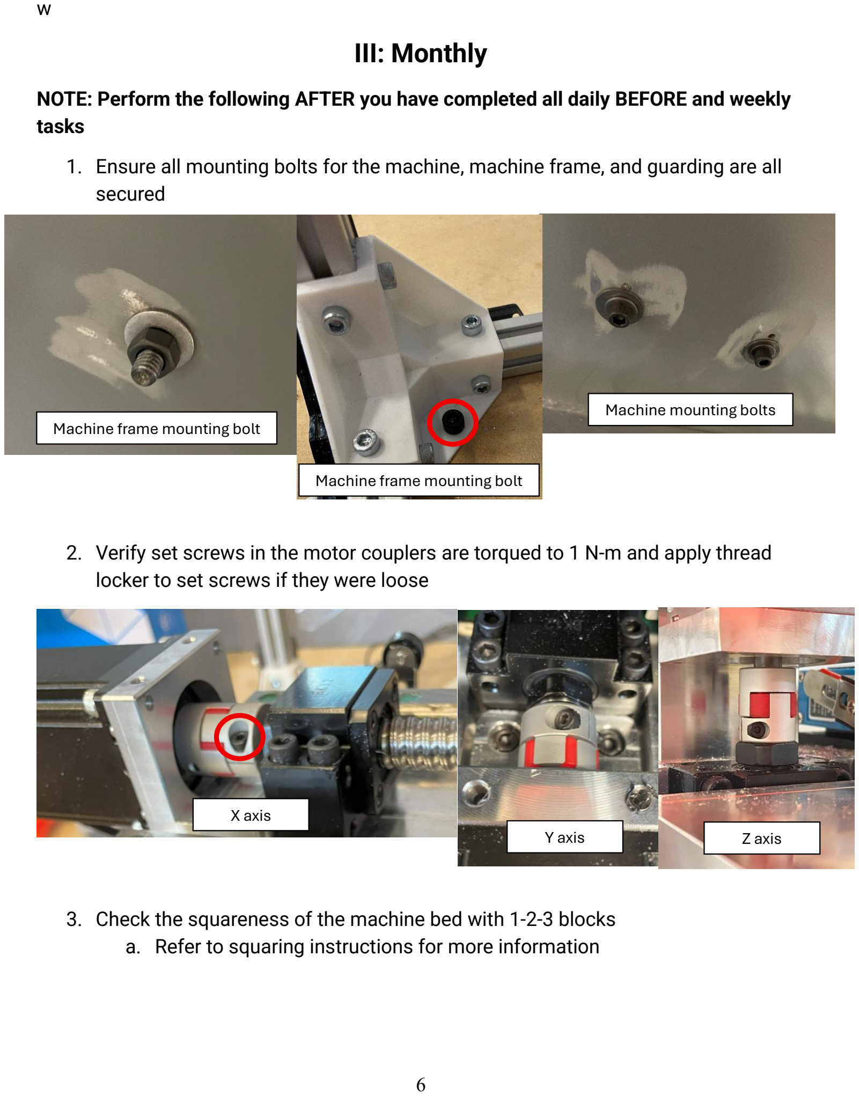
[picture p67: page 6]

w

NOTE: Perform the following AFTER you have completed all daily BEFORE and weekly tasks

1. Ensure all mounting bolts for the machine, machine frame, and guarding are all secured
2. Verify set screws in the motor couplers are torqued to 1 N-m and apply thread locker to set screws if they were loose
3. Check the squareness of the machine bed with 1-2-3 blocks
a. Refer to squaring instructions for more information

Machine frame mounting bolt

Machine frame mounting bolt

Machine mounting bolts

X axis
Y axis | Z axis

## IV: Semesterly

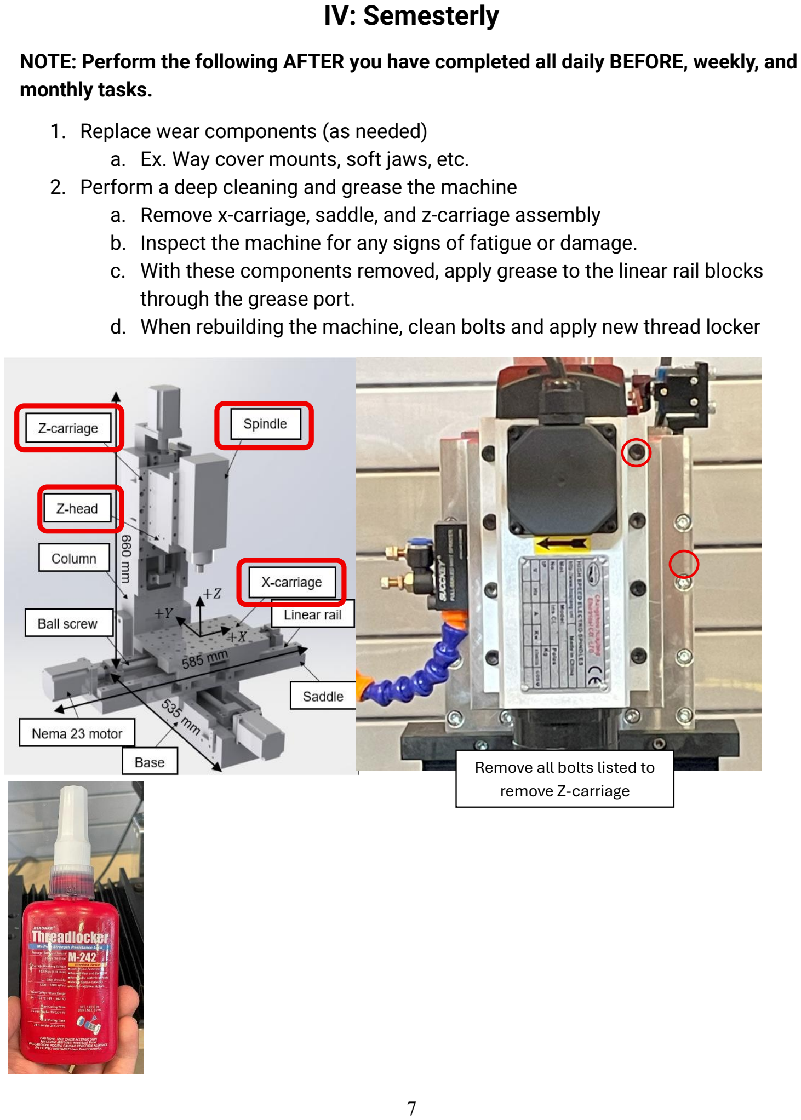
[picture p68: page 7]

NOTE: Perform the following AFTER you have completed all daily BEFORE, weekly, and monthly tasks.

1. Replace wear components (as needed)
a. Ex. Way cover mounts, soft jaws, etc.
2. Perform a deep cleaning and grease the machine
a. Remove x-carriage, saddle, and z-carriage assembly
b. Inspect the machine for any signs of fatigue or damage.
c. With these components removed, apply grease to the linear rail blocks through the grease port.
d. When rebuilding the machine, clean bolts and apply new thread locker

Remove all bolts listed to remove Z-carriage

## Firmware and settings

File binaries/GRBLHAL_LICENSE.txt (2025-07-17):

grblHAL - Firmware for Teensy 4.1  
Licensed under GNU General Public License v3.0 or later  
Source: https://github.com/grblHAL
Created with web-builder: https://svn.io-engineering.com:8443/

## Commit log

2025-07-16 bins and license
    [GRBLHAL_LICENSE.txt]
2025-07-17 update readme and licenses
    [GRBLHAL_LICENSE.txt]
2026-06-10 Added Enclosure and Software Instructions
    Enclosure instructions includes a hinge door mechanism with a plunger-style limit switch for the safety door.
    Software instructions are important for configuring the teensy 4.1 and for configuring the VFD to interact with the computer and spindle.
2026-06-10 Update Machine instructions.pdf
    Removed old enclosure section at the end of machine instructions, now it references Enclosure Instructions
2026-06-10 Update LC-CNC-BoM.xlsx
    Roller arm limit switches item count updated from one 2 pack to two 2 packs of roller arms.
    [LC-CNC-BoM.xlsx]
2026-06-10 Updated 3D Printing Files folder
    Includes all enclosure 3D printed parts and separates all 3D prints so users may configure their parts for their build plate as needed.
    [BigJig.STL, CNC Mill Door Handle.STEP, Connector cover bottom.STEP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]
2026-06-10 Edited 3D Printing Files
    Separated all 3D prints into their own separate files for users to configure on their build plate as desired.
    Removed discrepancies from the print quantities and the updated list is now Full List of 3D Prints.xlsx.
    [3PinDoveTailBracket025TEST.STEP, 5PinDoveTailBracket025TEST.STEP, BigJig.STL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]
2026-06-24 Added 3D Print Layout .3mf
    [Electrical Box 3D Print Layout.3mf, Enclosure Print Layout.3mf, LC-CNC-BoM.xlsx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]
